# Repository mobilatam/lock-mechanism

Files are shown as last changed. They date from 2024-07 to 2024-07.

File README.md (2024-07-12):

# Proyecto del Mecanismo de Bloqueo

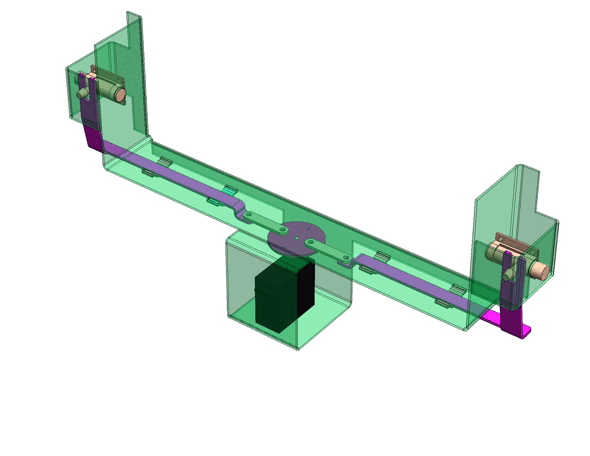
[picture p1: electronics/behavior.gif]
Behavior


Este proyecto incluye componentes de hardware y software, integrando diversas disciplinas como electrónica, mecánica y sistemas embebidos.

## Estructura del Proyecto

El proyecto está organizado en varios directorios y archivos clave:

- **.devcontainer**: Archivos de configuración para el contenedor de desarrollo.
- **.gitignore**: Especifica archivos y directorios que deben ser ignorados por Git.
- **CMakeLists.txt**: Archivo de configuración de CMake para compilar el proyecto.
- **dependencies.lock**: Archivo de bloqueo de dependencias del proyecto.
- **electronics**: Contiene esquemas, diseños de PCB, diseño de cajas, archivos STL y documentos relacionados.
- **main**: Código fuente y lógica principal de la aplicación.

## Funcionamiento

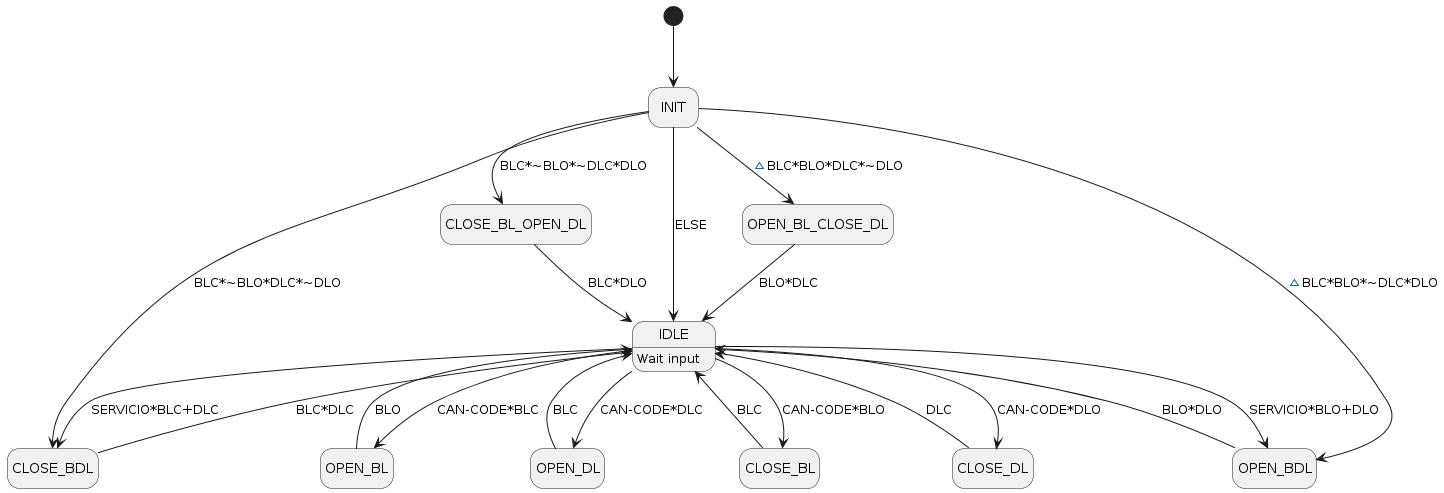
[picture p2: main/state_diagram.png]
Maquina de Estados


El programa inicializa las variables y el estado inicial en base al estado de los finales de carrera. Si el candado de la batería está cerrado y el de la puerta está abierto, el programa cierra el candado de la batería y abre el candado de la puerta. Si el candado de la batería presenta un error (cerrado y abierto al mismo tiempo) y el de la puerta está cerrado, el programa abre el candado de la batería y cierra el de la puerta. Si ninguna de estas condiciones se cumple, el programa entra en un estado de espera.

En el estado de espera, el programa aguarda una entrada que determine su próximo movimiento. Dependiendo de la entrada. Por ejemplo:
- Si se recibe la entrada CAN correspondiente y el candado de la batería está abierto, el programa cierra el candado de la batería.
- Si hay la entrada CAN correspondiente y el candado de la puerta está abierto, el programa cierra el candado de la puerta.

Además, hay condiciones especiales que dictan las transiciones del programa:
- Al activar el botón de servicio, si algun candado está abierto, el programa abre ambos candados.
- Al activar el botón de servicio, si algun candado esta cerrado, el programa cierra ambos candados.

El programa también maneja estados intermedios para la apertura y cierre de los candados de manera específica. Por ejemplo, un estado puede encargarse de cerrar el candado de la batería mientras abre el de la puerta, y otro puede hacer lo contrario. 

## Conexiones

Se diseñó un prototipo de PCB basado en la placa de desarrollo ESP32 de 38 pines.

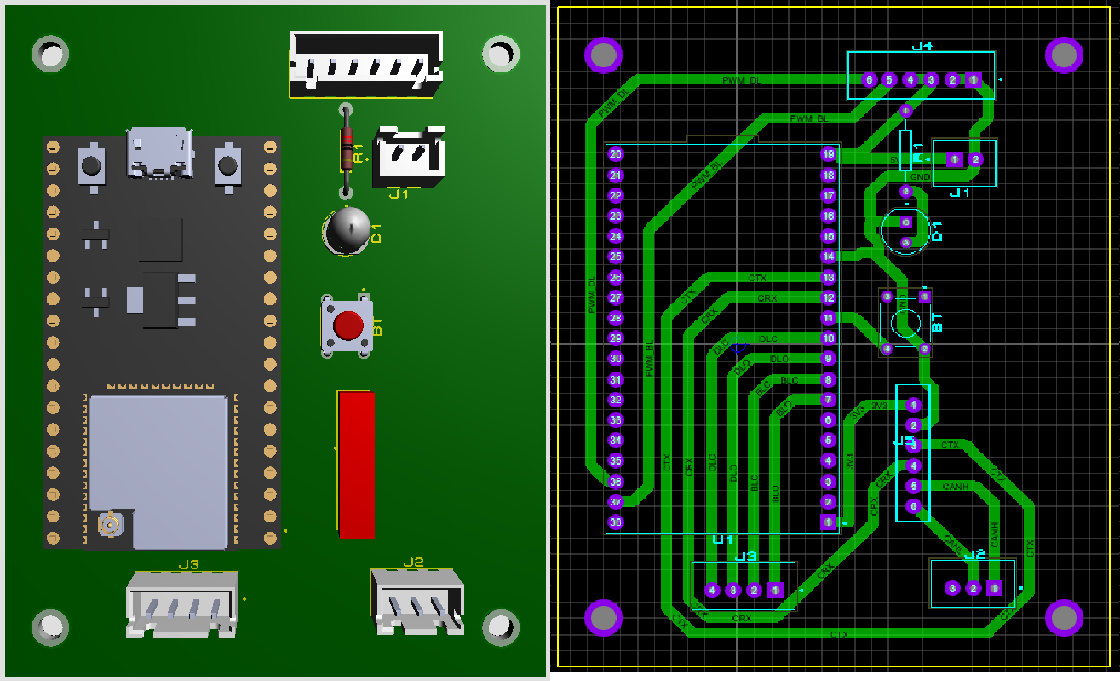
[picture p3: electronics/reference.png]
Referencia de placa PCB


Las conecciones del sistema se ilustran en el siguiente diagrama. 

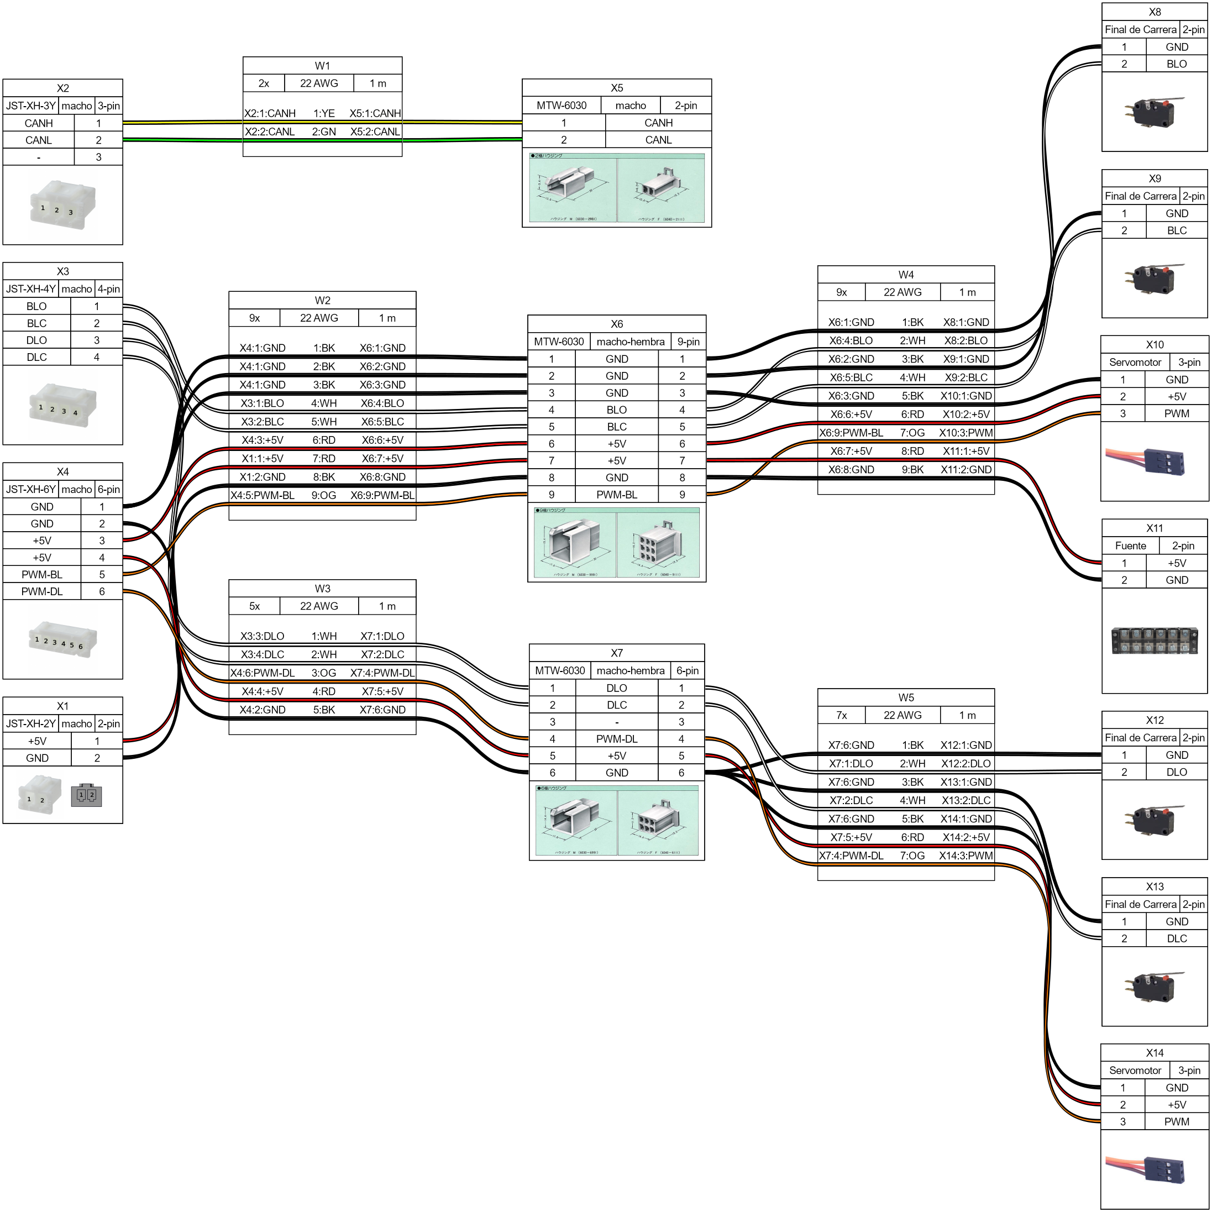
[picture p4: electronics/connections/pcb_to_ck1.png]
Conexiones de PCB a CK1


Significado de los acrónimos:
| Acrónimo | Description | Descripción |
|---|---|---|
| DLO | Door Lock Open | Apertura de la cerradura de la puerta |
| DLC | Door Lock Close | Cierre de la cerradura de la puerta |
| BLO | Battery Lock Open | Apertura de la cerradura de la batería |
| BLC | Battery Lock Close | Cierre de la cerradura de la batería |
| PWM-DL | PWM Door Lock | Cerradura de la puerta PWM |
| PWM-BL | PWM Battery Lock | Cerradura de la batería PWM |

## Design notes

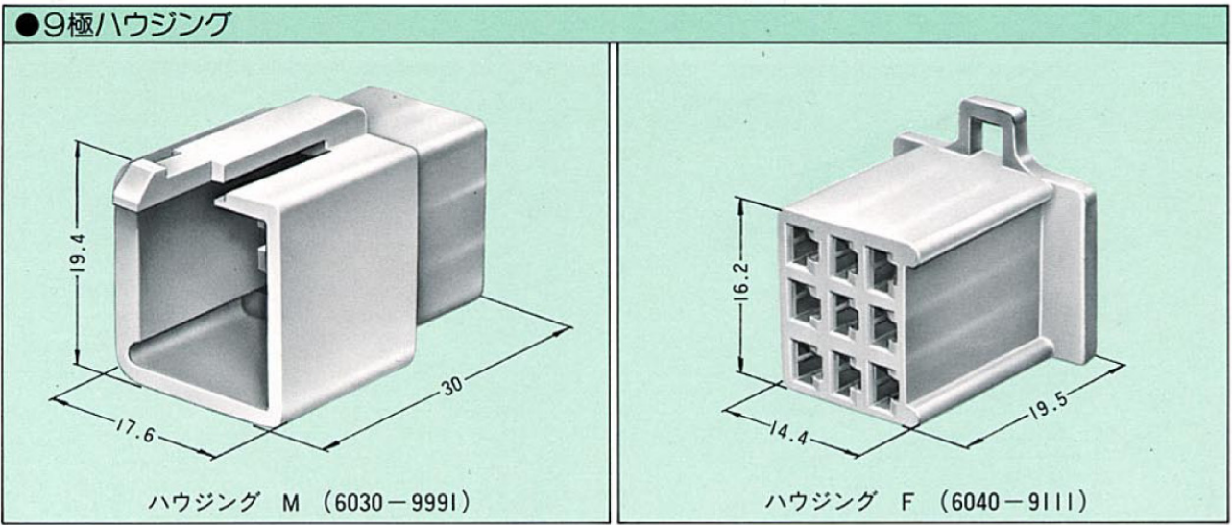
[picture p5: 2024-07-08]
electronics/connections/images/MTW-9.png

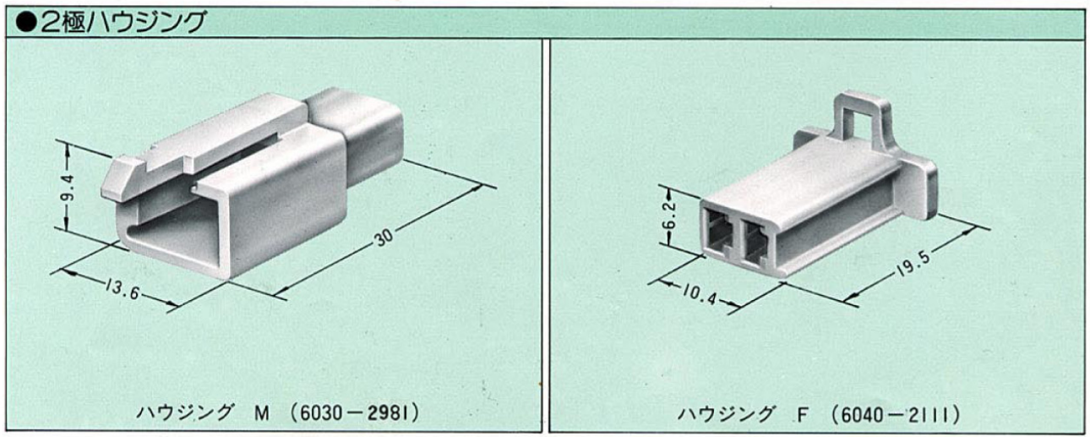
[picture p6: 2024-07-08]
electronics/connections/images/MTW-2.png

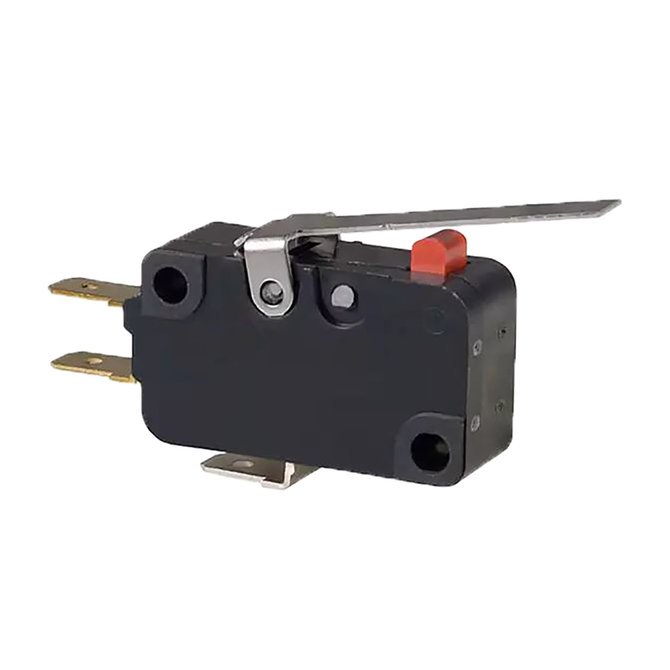
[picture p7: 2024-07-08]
electronics/connections/images/limit_switch.jpg

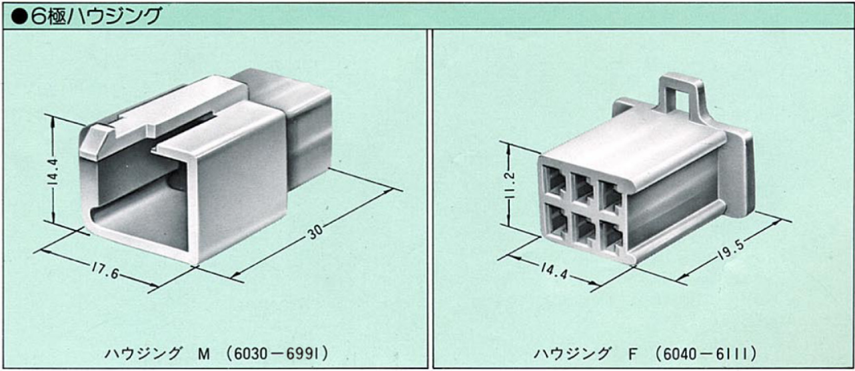
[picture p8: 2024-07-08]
electronics/connections/images/MTW-6.png

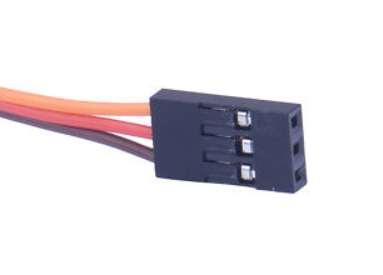
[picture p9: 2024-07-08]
electronics/connections/images/servo.png

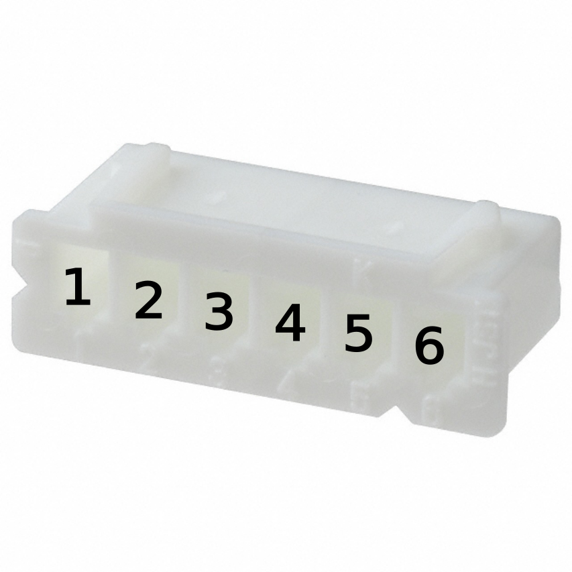
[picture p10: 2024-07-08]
electronics/connections/images/XHP-6.png

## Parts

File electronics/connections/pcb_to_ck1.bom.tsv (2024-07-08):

Id | Description | Qty | Unit | Designators
1 | Cable, 2 x 22 AWG | 1 | m | W1
2 | Cable, 5 x 22 AWG | 1 | m | W3
3 | Cable, 7 x 22 AWG | 1 | m | W5
4 | Cable, 9 x 22 AWG | 2 | m | W2, W4
5 | Connector, Final de Carrera, 2 pins | 4 |  | X12, X13, X8, X9
6 | Connector, Fuente, 2 pins | 1 |  | X11
7 | Connector, JST-XH-2Y, macho, 2 pins | 1 |  | X1
8 | Connector, JST-XH-3Y, macho, 3 pins | 1 |  | X2
9 | Connector, JST-XH-4Y, macho, 4 pins | 1 |  | X3
10 | Connector, JST-XH-6Y, macho, 6 pins | 1 |  | X4
11 | Connector, MTW-6030, macho, 2 pins | 1 |  | X5
12 | Connector, MTW-6030, macho-hembra, 6 pins | 1 |  | X7
13 | Connector, MTW-6030, macho-hembra, 9 pins | 1 |  | X6
14 | Connector, Servomotor, 3 pins | 2 |  | X10, X14

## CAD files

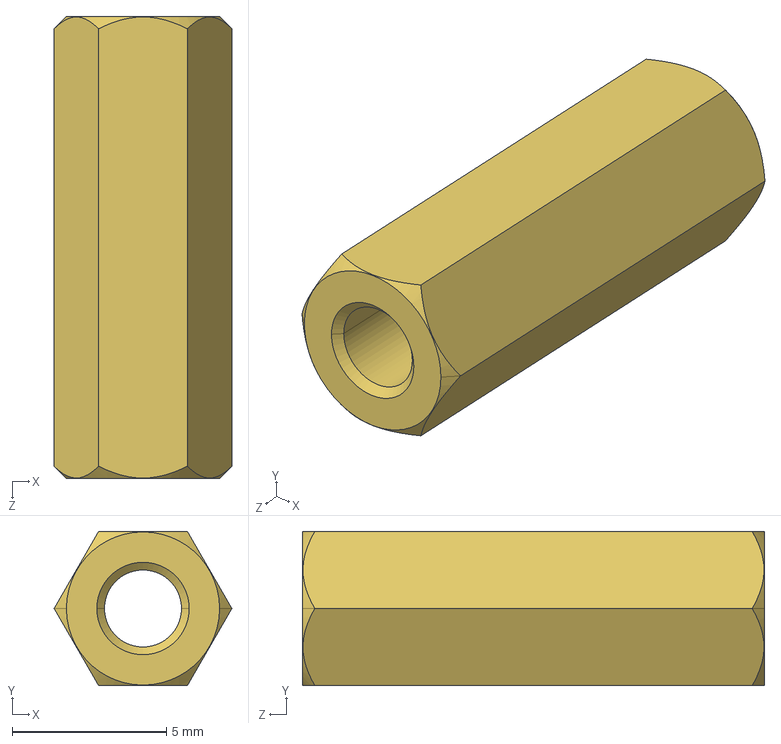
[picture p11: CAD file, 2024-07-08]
electronics/caja/M3_F_TO_F_15MM_STANDOFF.STEP
5.77 x 5.00 x 15.0 mm

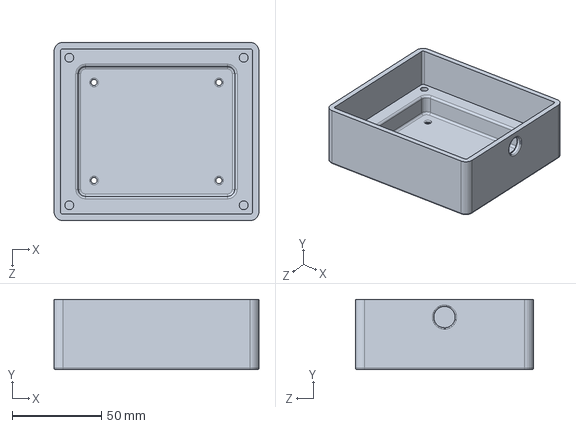
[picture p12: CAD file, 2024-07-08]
electronics/caja/cuerpo_caja.SLDPRT
115.0 x 39.5 x 100.0 mm

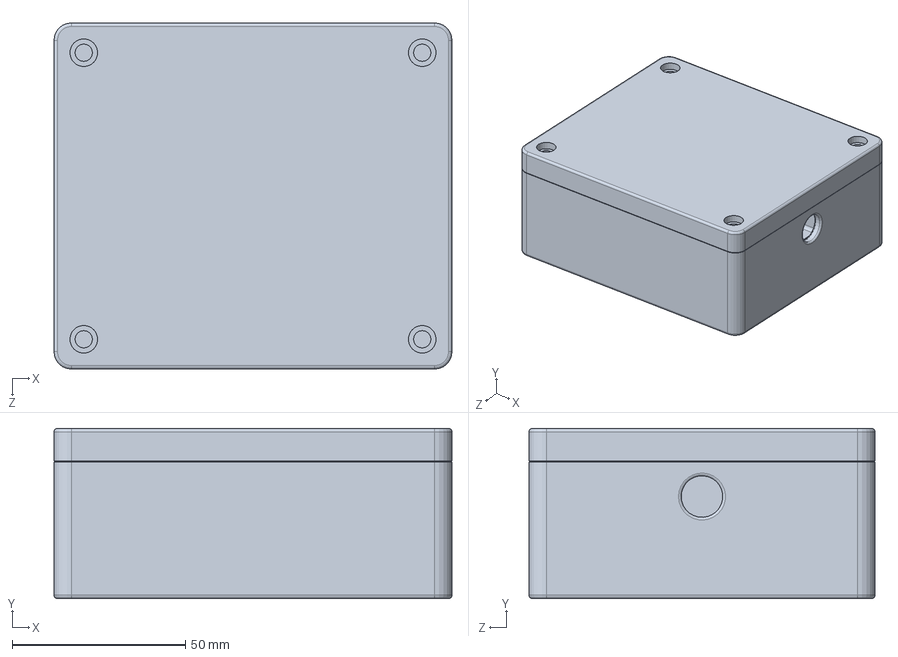
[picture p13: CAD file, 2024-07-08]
electronics/caja/caja.SLDPRT
115.0 x 49.2 x 100.0 mm

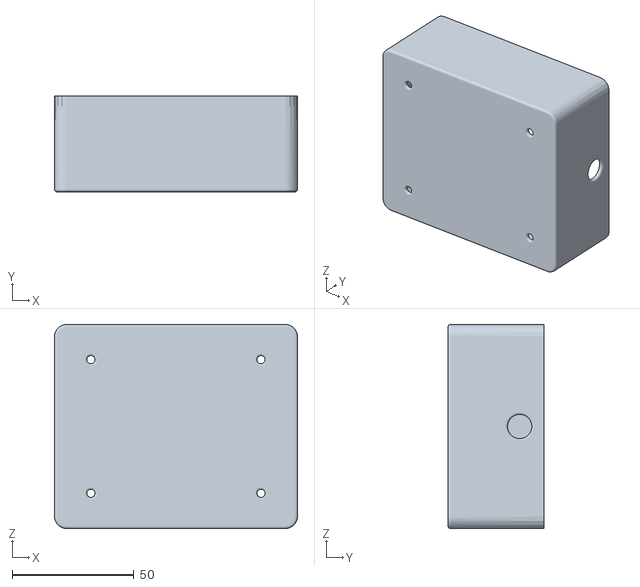
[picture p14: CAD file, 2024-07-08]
electronics/caja/caja_base.STL
100.0 x 39.5 x 84.0

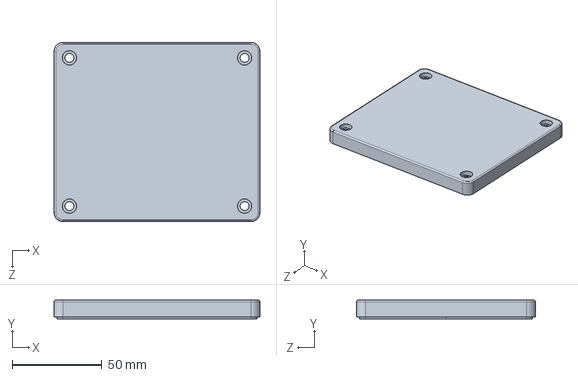
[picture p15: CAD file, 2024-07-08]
electronics/caja/tapa_caja.SLDPRT
115.0 x 10.5 x 100.0 mm

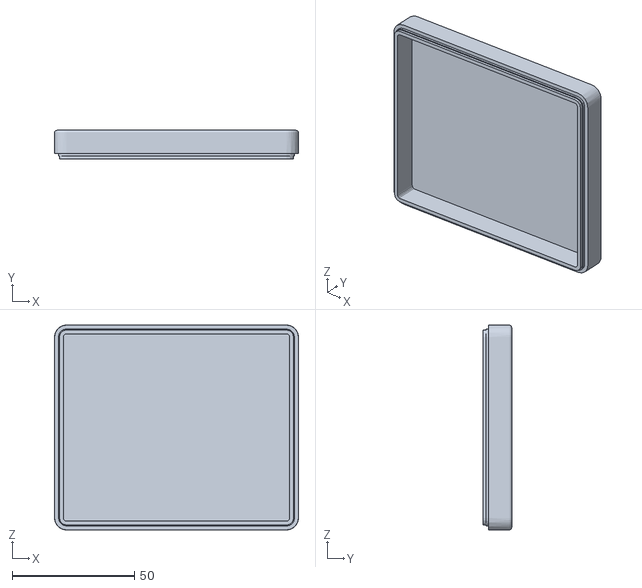
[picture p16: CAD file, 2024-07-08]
electronics/caja/caja_tapa.STL
100.0 x 11.7 x 84.0

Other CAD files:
electronics/caja/cuerpo_caja.STL
electronics/caja/tapa_caja.STL

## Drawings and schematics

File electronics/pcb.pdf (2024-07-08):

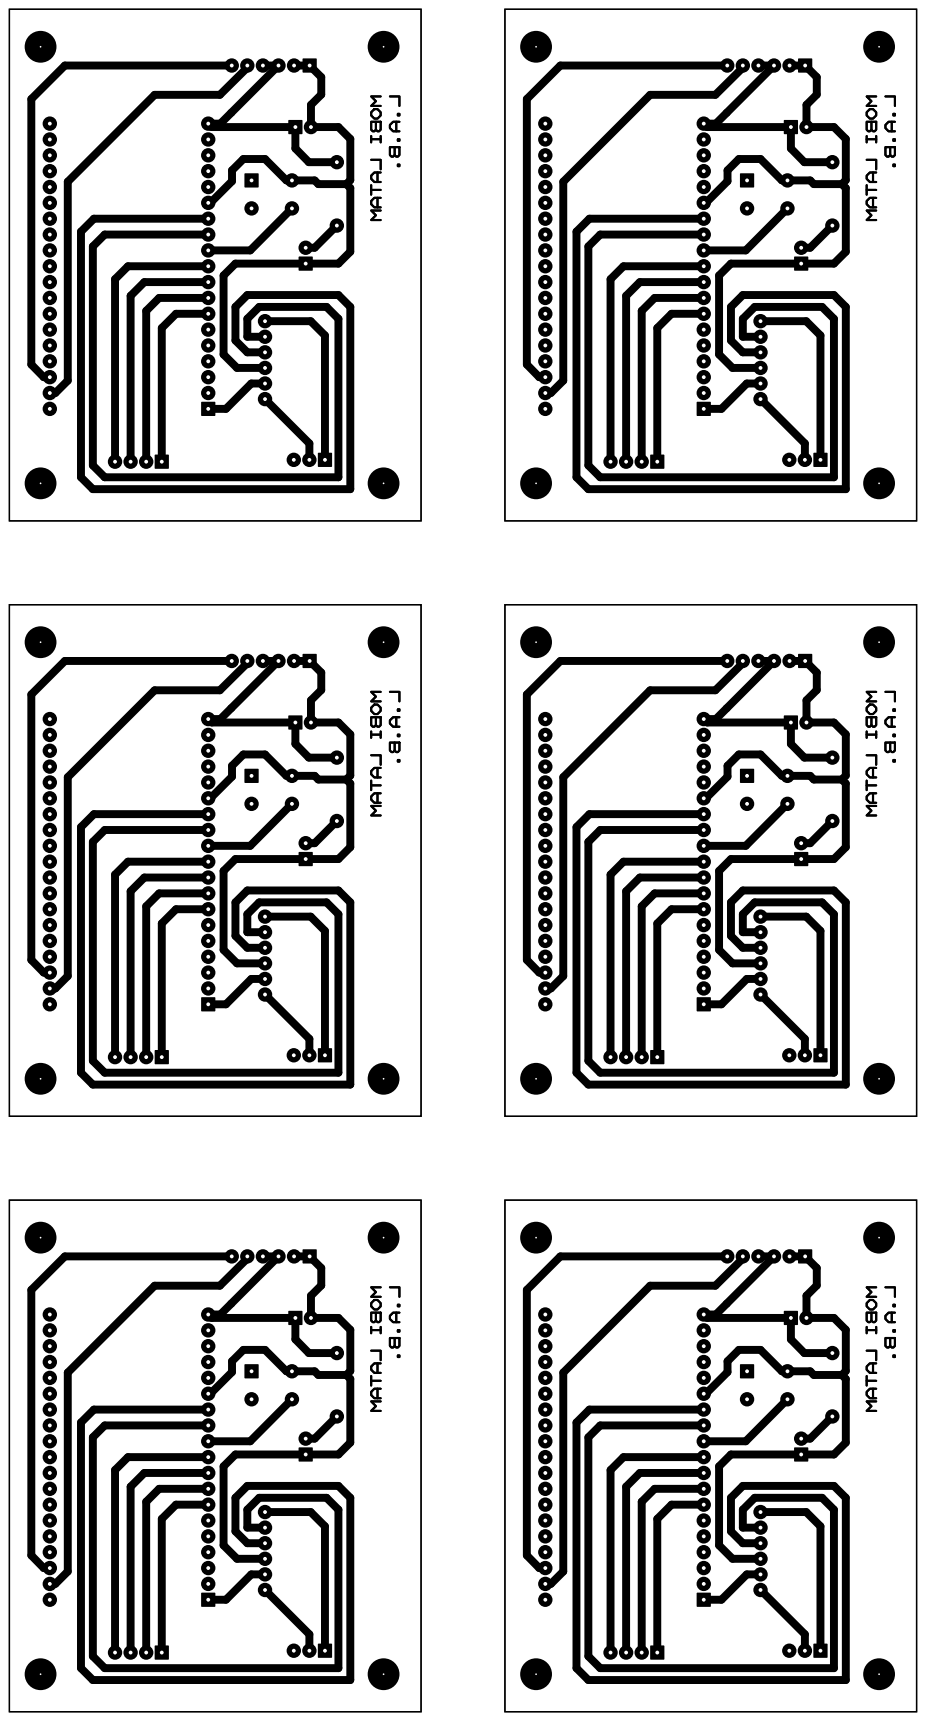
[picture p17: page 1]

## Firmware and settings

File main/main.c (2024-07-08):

/*******************************************************************************
 * @file        main.c
 * @author      Leonardo Acha Boiano
 * @date        01 Jul 2024
 * @brief       Main code CK1 lock and unlock mechanism
 * 
 * @note        This code is written in C and is used on an ESP32 38 PIN WROOM
 *
********************************************************************************/

#include "main.h"

twai_message_t message;

void app_main(void) {
    init_gpio();
    init_isr();
    // Configura el servomotor
    configure_servo();
    // Configura el controlador TWAI
    configure_twai();
    //Set initial state
    if ( //currentState=CLOSE_BL_OPEN_DL
        ~gpio_get_level(GPIO_BATTERY_LOCK_CLOSE)
        &gpio_get_level(GPIO_BATTERY_LOCK_OPEN)
        &gpio_get_level(GPIO_DOOR_LOCK_CLOSE)
        &~gpio_get_level(GPIO_DOOR_LOCK_OPEN)){
            lock_battery();
            unlock_door();
    }
    else if( //currentState=OPEN_BL_CLOSE_DL
        gpio_get_level(GPIO_BATTERY_LOCK_CLOSE)
        &~gpio_get_level(GPIO_BATTERY_LOCK_OPEN)
        &~gpio_get_level(GPIO_DOOR_LOCK_CLOSE)
        &gpio_get_level(GPIO_DOOR_LOCK_OPEN)){
            unlock_battery();
            lock_door();
    }
    else if ( //currentState=OPEN_BDL
        gpio_get_level(GPIO_BATTERY_LOCK_CLOSE)
        &~gpio_get_level(GPIO_BATTERY_LOCK_OPEN)
        &gpio_get_level(GPIO_DOOR_LOCK_CLOSE)
        &~gpio_get_level(GPIO_DOOR_LOCK_OPEN)){
            unlock_battery();
            unlock_door();
    }
    else if ( //currentState=CLOSE_BDL
        ~gpio_get_level(GPIO_BATTERY_LOCK_CLOSE)
        &gpio_get_level(GPIO_BATTERY_LOCK_OPEN)
        &~gpio_get_level(GPIO_DOOR_LOCK_CLOSE)
        &gpio_get_level(GPIO_DOOR_LOCK_OPEN)){ 
            lock_battery();
            lock_door();
    }

    ESP_LOGI(MAIN_TAG, "Inicializacion Completa");

    while (1) {
        //State machine logic
        // Intenta recibir un mensaje TWAI(CAN)
        if (twai_receive(&message, pdMS_TO_TICKS(10)) == ESP_OK) {
            handle_twai_message(message);
        }
    }
}

/********************************* END OF FILE ********************************/
/******************************************************************************/

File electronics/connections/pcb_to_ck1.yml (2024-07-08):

authors:
    Created:
      name: L. Acha Boiano
      date: 2024-07-04

connectors:
  X1:
    pincount: 2
    type: JST-XH-2Y
    subtype: macho
    pinlabels: [+5V, GND]
    image:
      src: images/XHP-2.png
      height: 70
  X2:
    pincount: 3
    type: JST-XH-3Y
    subtype: macho
    pinlabels: [CANH, CANL, -]
    image:
      src: images/XHP-3.png
      height: 100
  X3:
    pincount: 4
    type: JST-XH-4Y  
    subtype: macho
    pinlabels: [BLO, BLC, DLO, DLC]
    image:
      src: images/XHP-4.png
      height: 100
  X4:
    pincount: 6
    type: JST-XH-6Y
    subtype: macho
    pinlabels: [GND, GND, +5V, +5V, PWM-BL, PWM-DL]
    image:
      src: images/XHP-6.png
      height: 100
  
  X5:
    pincount: 2
    type: MTW-6030
    subtype: macho
    pinlabels: [CANH, CANL]
    image:
      src: images/MTW-2.png
      height: 100
  X6:
    pincount: 9
    type: MTW-6030
    subtype: macho-hembra
    pinlabels: [GND, GND, GND, BLO, BLC, +5V, +5V, GND, PWM-BL]
    image:
      src: images/MTW-9.png
      height: 100
  X7:
    pincount: 6
    type: MTW-6030
    subtype: macho-hembra
    pinlabels: [DLO, DLC, -, PWM-DL, +5V, GND]
    image:
      src: images/MTW-6.png
      height: 100
  X8:
    pincount: 2
    type: Final de Carrera
    pinlabels: [GND, BLO]
    image:
      src: images/limit_switch.jpg
      height: 100
  X9:
    pincount: 2
    type: Final de Carrera
    pinlabels: [GND, BLC]
    image:
      src: images/limit_switch.jpg
      height: 100
  X10:
    pincount: 3
    type: Servomotor
    pinlabels: [GND, +5V, PWM]
    image:
      src: images/servo.png
      height: 100
  X11:
    pincount: 2
    type: Fuente
    pinlabels: [+5V, GND]
    image:
      src: images/fuente.png
      height: 135
  X12:
    pincount: 2
    type: Final de Carrera
    pinlabels: [GND, DLO]
    image:
      src: images/limit_switch.jpg
      height: 100
  X13:
    pincount: 2
    type: Final de Carrera
    pinlabels: [GND, DLC]
    image:
      src: images/limit_switch.jpg
      height: 100
  X14:
    pincount: 3
    type: Servomotor
    pinlabels: [GND, +5V, PWM]
    image:
      src: images/servo.png
      height: 100

cables:
  W1:
    wirecount: 2
    length: 1
    gauge: 22 AWG
    colors: [YE, GN]

  W2:
    wirecount: 9
    length: 1
    gauge: 22 AWG
    colors: [BK, BK, BK, WH, WH, RD, RD, BK, OG]

  W3:
    wirecount: 5
    length: 1
    gauge: 22 AWG
    colors: [WH, WH, OG, RD, BK]

  W4:
    wirecount: 9
    length: 1
    gauge: 22 AWG
    colors: [BK, WH, BK, WH, BK, RD, OG, RD, BK]

  W5:
    wirecount: 7
    length: 1
    gauge: 22 AWG
    colors: [BK, WH, BK, WH, BK, RD, OG]

connections:
  -
    - X1: [1-2]
    - W2: [7-8]
    - X6: [7-8]
  -
    - X2: [1-2]
    - W1: [1-2]
    - X5: [1-2]

  -
    - X3: [1-2]
    - W2: [4-5]
    - X6: [4-5]
    
  -
    - X3: [3-4]
    - W3: [1-2]
    - X7: [1-2]

  -
    - X4: [1,1,1,3,5]
    - W2: [1-3,6,9]
    - X6: [1-3,6,9]
  
  -
    - X4: [2,4,6]
    - W3: [5,4,3]
    - X7: [6,5,4]

  -
    - X6: [1, 4]
    - W4: [1, 2]
    - X8: [1, 2]

  -
    - X6: [2, 5]
    - W4: [3, 4]
    - X9: [1, 2]
  
  -
    - X6: [3, 6, 9]
    - W4: [5, 6, 7]
    - X10: [1, 2, 3]

  -
    - X6: [7, 8]
    - W4: [8, 9]
    - X11: [1, 2]

  -
    - X7: [6, 1]
    - W5: [1, 2]
    - X12: [1, 2]

  -
    - X7: [6, 2]
    - W5: [3, 4]
    - X13: [1, 2]

  -
    - X7: [6, 5, 4]
    - W5: [5, 6, 7]
    - X14: [1, 2, 3]

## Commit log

2024-07-08 Initial commit: program files, wireviz connections, proteus ecad and solidworks cad files
    [M3_F_TO_F_15MM_STANDOFF.STEP, caja.SLDPRT, caja_base.STL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]
2024-07-08 led_strip library was unneded, so it was eliminated from build
2024-07-10 Modificacion al README para full width table
2024-07-10 Añadida imagen de referencia del prototipo de PCB
2024-07-31 pcb design modified based on jorge's observations
2024-07-31 servo LOGI messages added for testing, and duty cycles updated
